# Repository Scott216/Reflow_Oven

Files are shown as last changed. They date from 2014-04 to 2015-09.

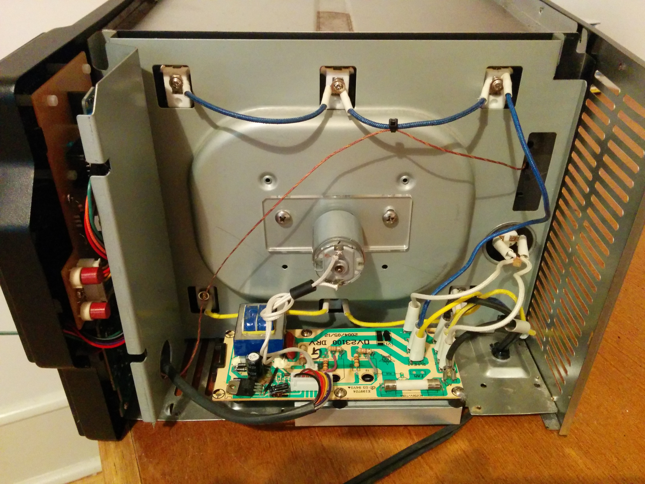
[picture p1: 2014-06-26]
Photos/Open Side.jpg

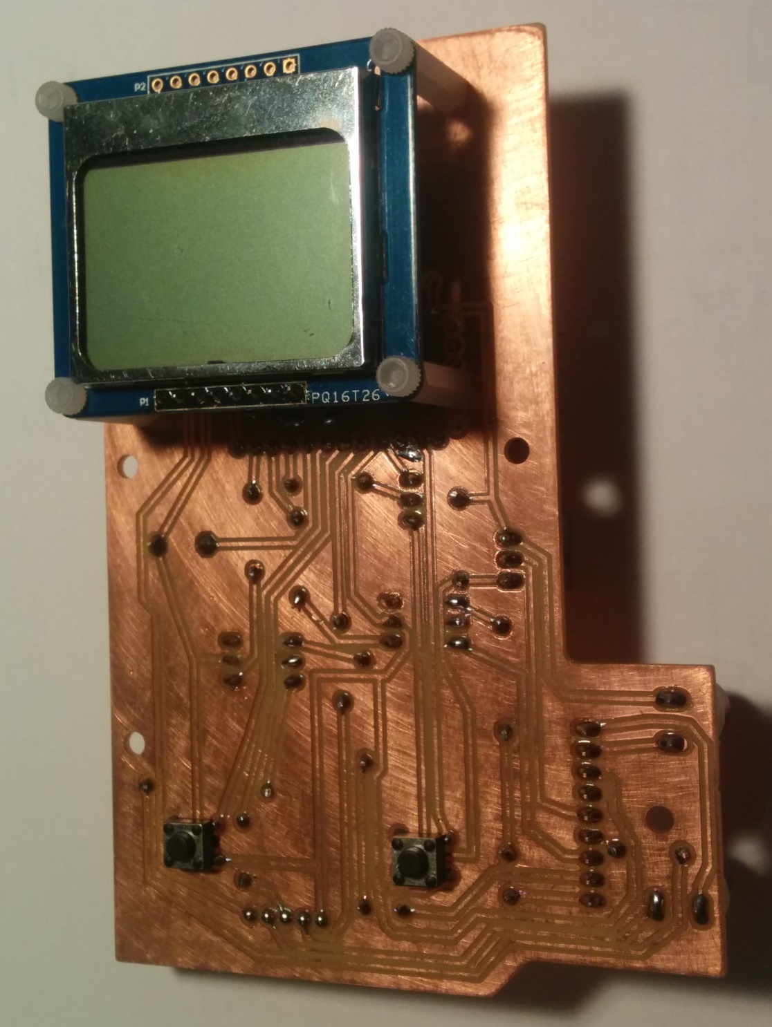
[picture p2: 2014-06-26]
Photos/PCB Traces.jpg

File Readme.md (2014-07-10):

Reflow Oven Controller <br>

I found a nice toaster oven when I when I was dropping some garbage off at our town's e-waste dumpster.  It was in excellent condition.  It has heating three heating elements on the top and three on the bottom . It had a microcontroller to control everything, so it was a bit more complex then a toaster with just a couple of knobs.  My plan was to remove the micro controller PCB and replace it with my own.  The heating elements are controlled by a couple of (triacs BTA26-600B).  I hadn't used triacs before and had to do a little research on them.  One unusual aspect of the toaster design is that the microcontroller board was floating on the 110 VAC line.  This means that the 5 VDC supply voltage was over 100 volts if measure from mains ground.  But the digital ground was only 5 volts less.  So to the micro controller board this was fine, but the whole PCB was essentially about 110 VAC.  I wasn't really comfortable with this, so I hacked the power supply board a bit so it output straight 5 volts.  it also output -9 volts. <br>

I wanted to continue to use the big start button from the front panel, so I took the original micro controller PCB and cut it in half to keep the start button and the LEDs that lit it up.  Then I soldered some wires in a header that connected to the button and LEDs.<br>

I designed a PCB with Cadsoft Eagle and milled it out on my [ShapeOko](http://www.shapeoko.com/) CNC router.  This was one of the first PCBs I did on the ShapeOko and it turned out pretty well (after a few revs). 
I had to figure out how to trigger the triacs properly.  At first I didn't realize I had to trigger when the AC voltage crossed zero volts, this cause some magic smoke to be released from one of the resistors.  This was easily fixed.  Then I got a couple of Fairchild [MOC3032](http://www.digikey.com/product-search/en?keywords=MOC3032M-ND) zero-crossover opto-couplers.  I had a Nokia 5110 display from Adafruit which was a great fit for the existing display window.  I used an Arduino [Pro-mini](http://www.sparkfun.com/products/11114) (3.3 v) from Sparkfun to control everything.  To measure the temperature I have a [thermocouple](http://www.adafruit.com/products/270) from Adafruit and Adafruit's [thermocouple amplifier](http://www.adafruit.com/products/269).  <br>

For the Arduino code I started with code from here: http://github.com/CvW/Reflow-Oven-Controller/, which is based on code from [Rocketscream](http://github.com/rocketscream/Reflow-Oven-Controller).  There was a bug in the debounce code I fixed and I replaced the MAX6675 with MAX31855 thermocouple amplifier.   There a bunch of other little changes, nothing major.  The code has two solder temperature profiles that you can choose between (by pressing the bake button) - one for leaded paste and one for a low-temp paste <br>

This toaster is not a convection toaster where it circulates the air around, but I thought this would be a nice feature. So I used a little motor that I salvaged from an inkjet printer to power a 3.5 inch aluminum fan blade I ordered from McMaster (17545K63).  I used a 3/16 bronze flange busing (McMaster 9440T63) to support the brass shaft through the sheet metal side. The fan is a bit noisy, but works pretty well.  Since the reflow oven isn't an that long, not a lot of heat is conducted to the motor from the shaft. <br>  

I would like to have an interior light to illuminate the PCB as it's being reflowed, but I haven't figured out how to do that yet. <br>

You can see some pictures on [flickr](https://www.flickr.com/photos/37101040@N00/sets/72157645550432296/) or in the \photos directory of the repo. <br>

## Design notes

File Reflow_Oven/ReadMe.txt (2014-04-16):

Reflow Oven Controller
Based on  https://github.com/CvW/Reflow-Oven-Controller/blob/master/reflowOvenController.pde
Which is based on http://github.com/rocketscream/Reflow-Oven-Controller

BoM

1x Arduino Pro-Mini 3.3 volts https://www.sparkfun.com/products/11114
1x LCD Display monochrome 84x84 http://www.adafruit.com/products/338
1x Red LED
1x Green LED
1x Solid State Relay
1x Fuse Holder
1x Fuse
1x Thermocouple Breakout board http://www.adafruit.com/products/269
1x Thermocouple probe
1x Contactless IR sensor http://www.adafruit.com/products/1747
2x pushbuttons
1x Diode for motor noise reduction
1x Cap for motor noise reduction
1x MOSFET to run motor
2x Strip heter, McMaster 3619K831
2ft Oven Wire
Calcium Silicate Insulation McMaster 9353K32 9353K31
1x High temp gasketing adhesive McMaster 7573A63
1x DC Motor
1x RC boat prop, metal
1x shaft Coupling
1x Thermistor Digikey KC024N-ND
1x AC/DC Converter Digikey 102-2386-ND, data sheet http://www.cui.com/product/resource/vsk-s5.pdf
1x 5v to 3v voltage regulator - might be able to use regulator in Pro-Mini
1x 1uF cap for AC/DC supply
1x 47uF cap for AC/DC supply
1x MOV Varistor
1x Relay for heater Digikey CLA394-ND, 6 amp, Input: 1.2 volts 1.5mA  Datasheet http://www.clare.com/home/pdfs.nsf/www/CPC1907B.pdf/$file/CPC1907B.pdf
1x 1.5k Resistor for Relay
1x Buzzer
2x I2C pullup resistors

To Do: 
See if buzzer works on 3v

PCB Design
Have 4 port terminal block in case you want to use IR sesnsor, it's I2C
Power thermocouple breakout board on 3 volt Vo pin - verify this will work

1       1       1       0
26      130.00          27.00           1       1       1       0
27.00   30.00   -0.60   0       -60
27      130.00          26.75           1       1       1       0
28      130.00          26.50           1       1       1       0
29      130.00          26.50           1       1       1       0
30      130.00          26.25           1       1       1       0
31      130.00          26.00           1       1       1       0
26.00   27.00   -0.20   0       -20
32      130.00          26.00           1       1       1       0
33      130.00          26.00

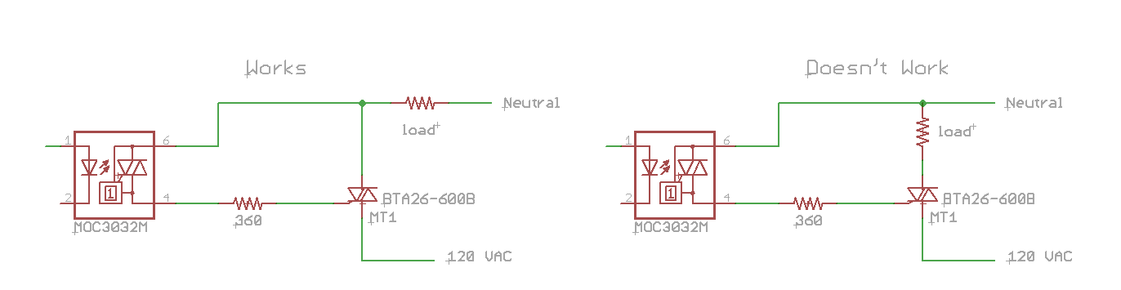
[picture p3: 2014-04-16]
Zero Crossing Triac Cuircuit 2.png

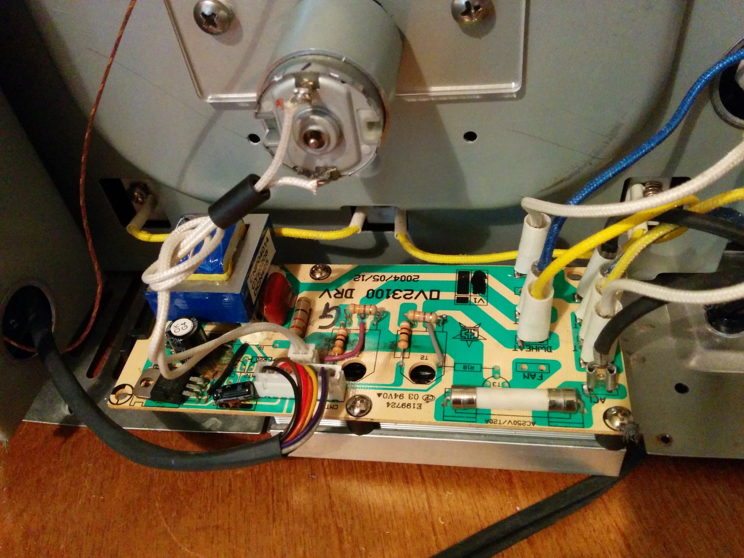
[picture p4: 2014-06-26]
Photos/Power Supply.jpg

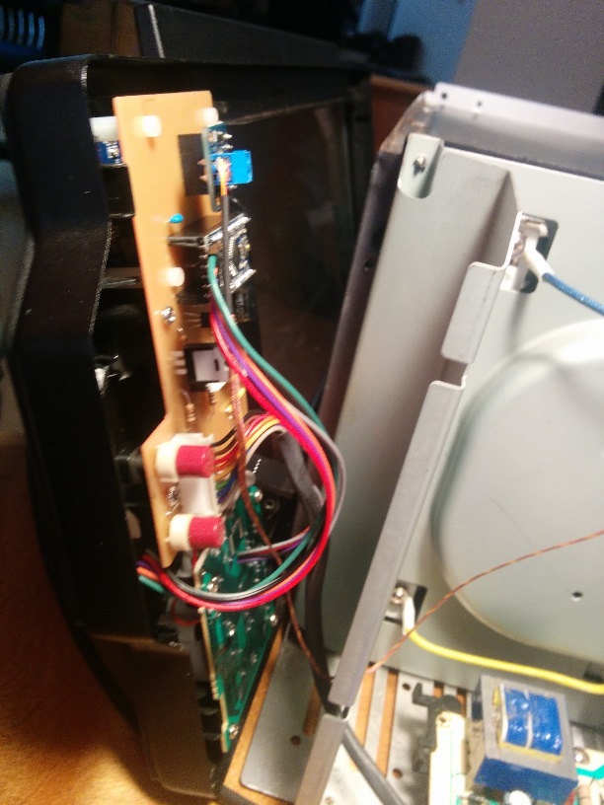
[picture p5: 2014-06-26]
Photos/Mounted PCB 2.jpg

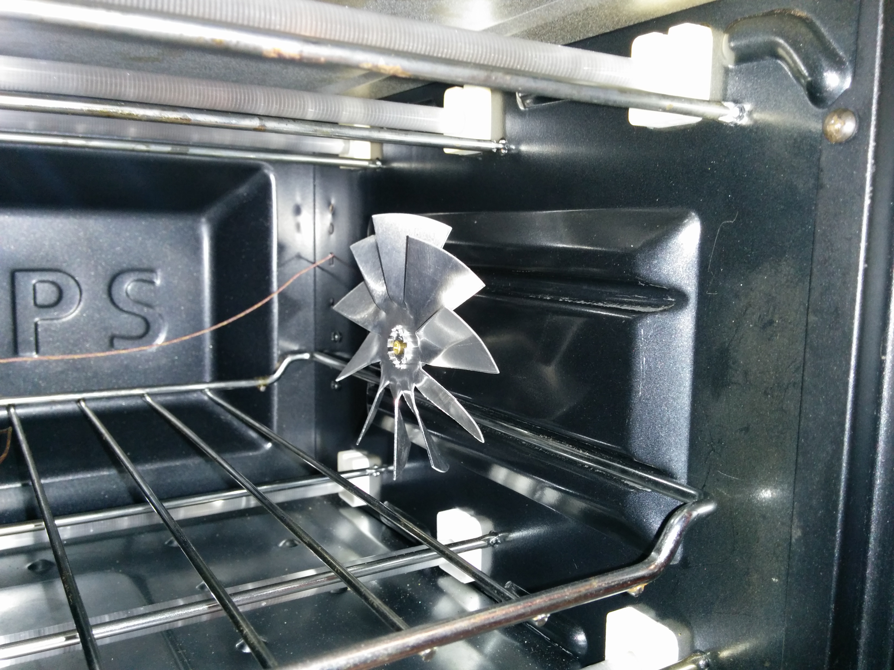
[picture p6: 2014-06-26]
Photos/Convection Fan.jpg

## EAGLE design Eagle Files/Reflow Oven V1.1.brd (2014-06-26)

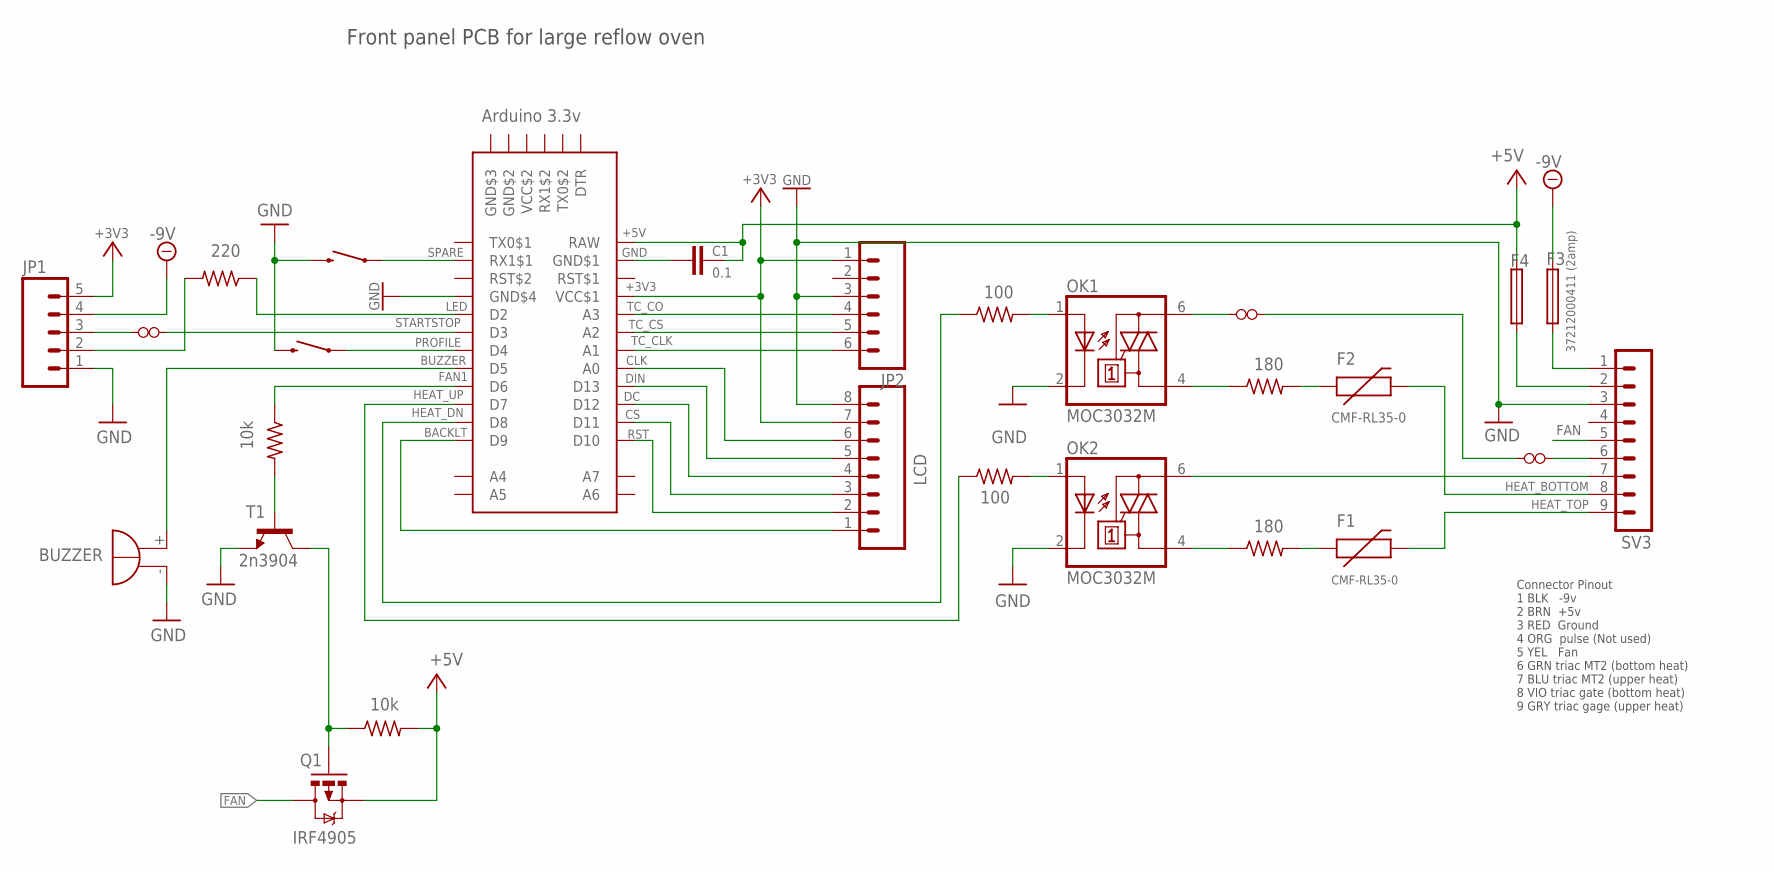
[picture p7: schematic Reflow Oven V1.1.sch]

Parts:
BUZZER: F/HMB
C1: 0.1; CAP-PTH-SMALL
F1, F2: CMF-RL35-0; PTC
F3, F4: 37212000411 (2amp); 19560
JP1: M05PTH; 1X05
JP2: M06SIP; 1X06
LCD: M081X08; 1X08
OK1, OK2: MOC3032M; DIL06
PROFILE: SWITCH-MOMENTARY-2PTH; TACTILE-PTH
Q1: IRF4905; TO220V
R2, R5: 100; 0207/10
R3, R4: 180; 0207/12
R11, R13: 10k; 0207/10
R12: 220; 0207/10
SPARE: SWITCH-MOMENTARY-2PTH; TACTILE-PTH
SV3: MA09-1
T1: 2n3904; TO92-EBC
U$1, U$4: JUMPER0.3_INCH; JUMPER_0.3
U$2: Arduino 3.3v; ARDUINO_PRO_MINI
U$5: JUMPER0.7INCH; JUMPER_0.7

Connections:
+3V3: JP1.5, JP2.1, LCD.7, U$2.VCC$1
+5V: C1.1, F4.2, Q1.3 (S), R13.2, U$2.RAW
-9V: F3.2, JP1.4
BACKLT: LCD.1, U$2.D9
BUZZER: BUZZER.+, U$2.D5
CLK: LCD.6, U$2.A0
CS: LCD.3, U$2.D11
DC: LCD.4, U$2.D12
DIN: LCD.5, U$2.D13
FAN: Q1.2 (D), SV3.5
FAN1: R11.1, U$2.D6
F_GATE: Q1.1 (G), R13.1, T1.C
GND: BUZZER.-, JP1.1, JP2.3, LCD.8, OK1.2 (C), OK2.2 (C), PROFILE.3 (2), SPARE.3 (2), SV3.3, T1.E, U$2.GND$4
GND2: C1.2, U$2.GDN$1 (GND$1)
GND$2: U$2.GND$2
GND$3: U$2.GND$3
HEAT_BOTTOM: F2.P$2 (2), SV3.8
HEAT_DN: R5.1, U$2.D8
HEAT_TOP: F1.P$2 (2), SV3.9
HEAT_UP: R2.1, U$2.D7
LED: R12.1, U$2.D2
unnamed: OK1.4 (A1), R3.1
unnamed: OK2.6 (A2), SV3.7
unnamed: F2.P$1 (1), R3.2
unnamed: F4.1, SV3.2
unnamed: F1.P$1 (1), R4.2
unnamed: OK2.4 (A1), R4.1
unnamed: U$1.P$1, U$5.P$2
unnamed: SV3.6, U$1.P$2
unnamed: OK1.1 (A), R5.2
unnamed: OK1.6 (A2), U$5.P$1
unnamed: OK2.1 (A), R2.2
unnamed: JP1.3, U$4.P$1
unnamed: F3.1, SV3.1
unnamed: R11.2, T1.B
unnamed: JP1.2, R12.2
PROFILE: PROFILE.1, U$2.D4
RST: LCD.2, U$2.D10
SPARE: SPARE.1, U$2.RX1$1
STARTSTOP: U$2.D3, U$4.P$2
TC_CLK: JP2.6, U$2.A1
TC_CO: JP2.4, U$2.A3
TC_CS: JP2.5, U$2.A2
VCC$2: U$2.VCC$2

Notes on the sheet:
Front panel PCB for large reflow oven
Connector Pinout 1 BLK -9v 2 BRN +5v 3 RED Ground 4 ORG pulse (Not used) 5 YEL Fan 6 GRN triac MT2 (bottom heat) 7 BLU triac MT2 (upper heat) 8 VIO triac gate (bottom heat) 9 GRY triac gage (upper heat)

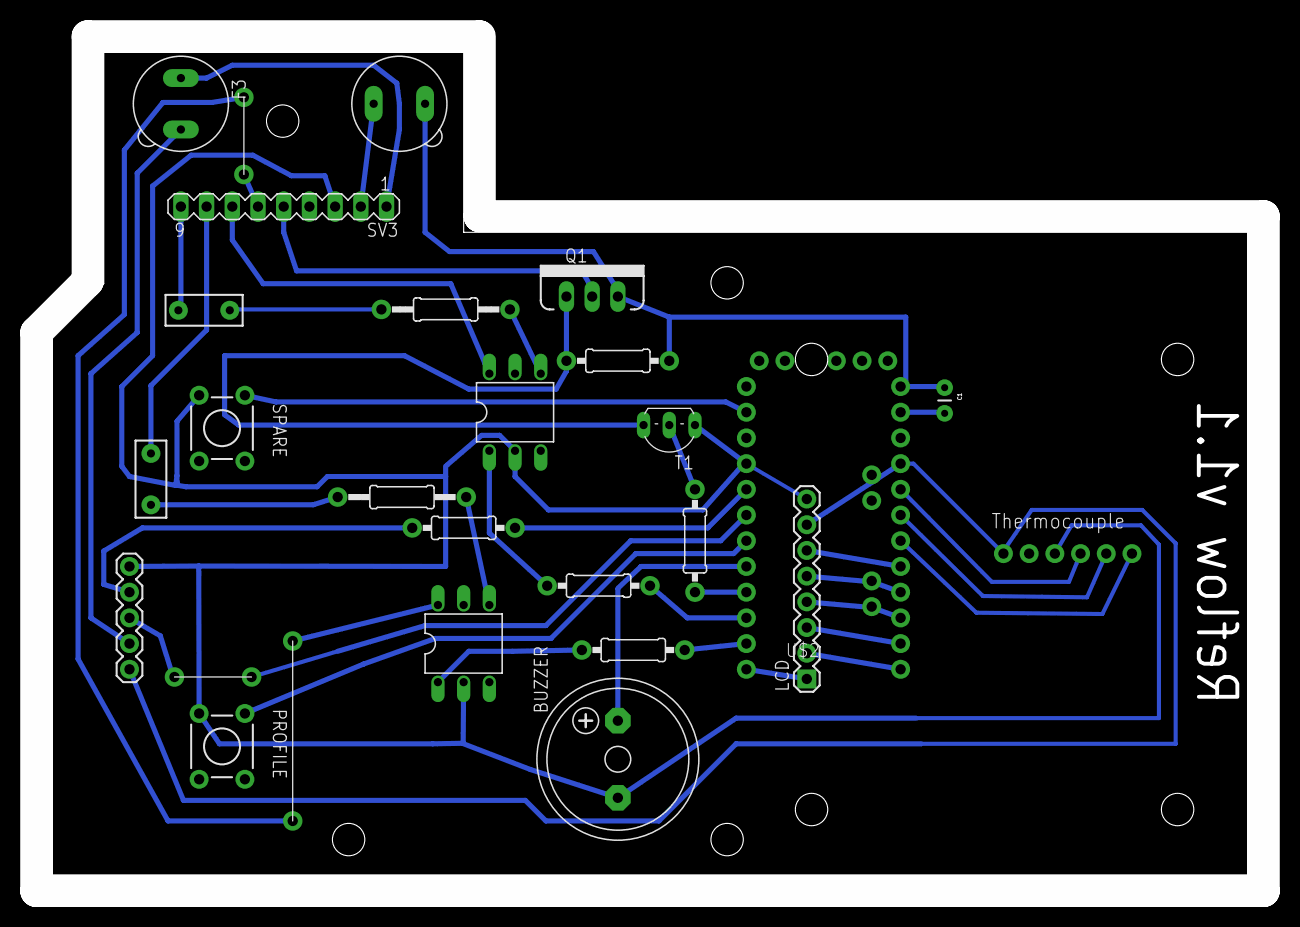
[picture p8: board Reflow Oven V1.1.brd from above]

Board: 2 copper layers, 121.3 x 84.5 mm, 27 parts (1 on the bottom side), 41 nets.

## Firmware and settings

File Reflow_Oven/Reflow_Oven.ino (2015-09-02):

// Uses Arduino ProMini 3.3 volts

// to do
// had hall effect sensor to detect fan current and shut down if too high - maybe
// put a switch on the fan - maybel
// PCB Circuit swaps D2 and D4
// Put limits on setpoints so they cont go to high if there is a problem

/*******************************************************************************
 * Title: Reflow Oven Controller
 * Company: Rocket Scream Electronics
 * Original Author: Lim Phang Moh
 * Website: www.rocketscream.com
 * 
 * Brief
 * =====
 * This is an example firmware for our Arduino compatible reflow oven controller. 
 * The reflow curve used in this firmware is meant for lead-free profile 
 * (it's even easier for leaded process!). You'll need to use the MAX31855 
 * library for Arduino if you are having a shield of v1.60 & above which can be 
 * downloaded from our GitHub repository. Please check our wiki 
 * http://www.rocketscream.com/wiki for more information on using this piece of code 
 * together with the reflow oven controller shield. 
 *
 * Temperature (Degree Celcius)                 Magic Happens Here!
 * 245-|                                               x  x  
 *     |                                            x        x
 *     |                                         x              x
 *     |                                      x                    x
 * 200-|                                   x                          x
 *     |                              x    |                          |   x   
 *     |                         x         |                          |       x
 *     |                    x              |                          |
 * 150-|               x                   |                          |
 *     |             x |                   |                          |
 *     |           x   |                   |                          | 
 *     |         x     |                   |                          | 
 *     |       x       |                   |                          | 
 *     |     x         |                   |                          |
 *     |   x           |                   |                          |
 * 30 -| x             |                   |                          |
 *     |<  60 - 90 s  >|<    90 - 120 s   >|<       90 - 120 s       >|
 *     | Preheat Stage |   Soaking Stage   |       Reflow Stage       | Cool
 *  0  |_ _ _ _ _ _ _ _|_ _ _ _ _ _ _ _ _ _|_ _ _ _ _ _ _ _ _ _ _ _ _ _ _ _ _ _ 
 *                                 Time (Seconds)
 *
 * Kester's standard leaded profile http://www.kester.com/kester-content/uploads/2013/06/Standard_Profile.pdf
 * This firmware owed very much on the works of other talented individuals as
 * follows:
 * ==========================================
 * Brett Beauregard (www.brettbeauregard.com)
 * ==========================================
 * Author of Arduino PID library. On top of providing industry standard PID 
 * implementation, he gave a lot of help in making this reflow oven controller 
 * possible using his awesome library.
 *
 *
 * Disclaimer
 * ==========
 * Dealing with high voltage is a very dangerous act! Please make sure you know
 * what you are dealing with and have proper knowledge before hand. Your use of 
 * any information or materials on this reflow oven controller is entirely at 
 * your own risk, for which we shall not be liable. 
 *
 * Licences
 * ========
 * This reflow oven controller hardware and firmware are released under the 
 * Creative Commons Share Alike v3.0 license
 * http://creativecommons.org/licenses/by-sa/3.0/ 
 * You are free to take this piece of code, use it and modify it. 
 * All we ask is attribution including the supporting libraries used in this 
 * firmware. 
 *
 *
 * Source: http://github.com/CvW/Reflow-Oven-Controller/blob/master/reflowOvenController.pde
 * Which is based on http://github.com/rocketscream/Reflow-Oven-Controller
 *
 * Info on PID: http://brettbeauregard.com/blog/2011/04/improving-the-beginners-pid-introduction/
 * Build instructions: http://www.rocketscream.com/blog/portfolio-item/reflow-controller-shield
 *
 *
 * Rocket Scream Revisions
 * Revision  Description
 * ========  ===========
 * 1.20			Adds supports for v1.60 (and above) of Reflow Oven Controller 
 *           Shield:
 *					  - Uses MAX31855KASA+ chip and pin reassign (allowing A4 & A5 (I2C)
 *             to be used for user application).
 *					  - Uses analog based switch (allowing D2 & D3 to be used for user 
 *						  application).	
 *						Adds waiting state when temperature too hot to start reflow process.
 *						Corrected thermocouple disconnect error interpretation (MAX6675).
 * 1.10      Arduino IDE 1.0 compatible.
 * 1.00      Initial public release.
 *
 *
 * CvW Revisions
 * Revision  Description
 * ========  ===========
 * 1.20      Added option for lead solder profile, Enabled fan motor, added error message
 * 1.10      Arduino IDE 1.0 compatible.
 * 1.00      Initial public release.
 *
 * Scott216 Revisions
 * Revision  Description
 * ========  ===========
 * 1.21      Started with CvW version 1.2 and replaced MAX6675 library with Adafruit_MAX31855, changed some formatting
 * 1.22      Moved LCD display code to separate function, added NAN error checking on thermocouple, changed profiles to leaded and low temp, changed LED output so HIGH is on
 * 1.23      Took typedef out of enum, moved buttons to D0 & D1 because of I2C conflict, changed I2C library.  Removed debounce for button #2, it was causing problems where btn1 would make btn2 code run
 * 1.24      Updated profile temperatures, moved some code out of loop() into functions, removed 2 line LCD code.  Added seconds and rate to LCD display.  Changed some variables.
 * 1.25      Change pins for Pro-Mini, changed C/Sec to average over 5 seconds
 * 1.26      Changed display to Nokia 5110, tested for negative rate change so it will display properly
 * 1.27      Changed I/O pins, added pin for LED backlight
 * 1.28      When calling for heat, top and bottom heaters will altenrate coming on.
 * 1.29      Reversed LED output (Low = on), made display text 3 lines.  Changed fan from digital to PWM
 * 1.30      Buzzer sounds and each stage in reflow.  Adjusted heat on to better balance top and bottom heaters, display profile when idle
 * 1.31      Added mircostepping temp target to pre-heat stage, show setpoint temp in display
 * 1.32      Fan was not turning off after cool period was over, should be fixed now 
 * 1.33      Changed contrast, moved inputs to match new PCB
 * 1.34      Adjusted contrast
 * 1.35      Adjusted contrast again, added more beeps when cooling stage starts 
 * 1.36      Changed constast from 40 to 50.  Added FAN_OFF constant
 * 1.37      Added max setpoint to prevent run-away temp, renamed global variables
 
 *******************************************************************************/
#define VERSION  "ver 1.37"

#include "Adafruit_MAX31855.h"  // http://github.com/adafruit/Adafruit-MAX31855-library
#include "PID_v1.h"             // http://github.com/br3ttb/Arduino-PID-Library/
#include "Adafruit_GFX.h"       // https://github.com/adafruit/Adafruit-GFX-Library
#include "Adafruit_PCD8544.h"   // http://github.com/adafruit/Adafruit-PCD8544-Nokia-5110-LCD-library


// ***** TYPE DEFINITIONS *****
enum reflowState_t
{
  REFLOW_STATE_IDLE,
  REFLOW_STATE_PREHEAT,
  REFLOW_STATE_SOAK,
  REFLOW_STATE_REFLOW,
  REFLOW_STATE_COOL,
  REFLOW_STATE_COMPLETE,
  REFLOW_STATE_ERROR
};

enum reflowStatus_t
{
  REFLOW_STATUS_OFF,
  REFLOW_STATUS_ON
};

enum debounceState_t
{
  DEBOUNCE_STATE_IDLE,
  DEBOUNCE_STATE_CHECK,
  DEBOUNCE_STATE_RELEASE
} ;

enum printData_t { PRINT_HEADER, PRINT_DATA};
  
// ***** CONSTANTS *****
#define TEMPERATURE_ROOM             50   // Temp must be below this to start a new reflow
#define SENSOR_SAMPLING_TIME       1000
#define PREHT_TEMPERATURE_STEP        5   // increment pre-heat temp in 5 degree steps
#define SOAK_TEMPERATURE_STEP         5   // increment soak temp in 5 degree steps
#define PREHT_MICRO_PERIOD         4250   // set new pre-heat target temp every 4-1/4 seconds
#define SOAK_MICRO_PERIOD          9000   // set new soak target temp evey 9 seconds
#define DEBOUNCE_PERIOD_MIN          50
#define MAX_ALLOWED_TEMP            250  // Max temp oven is allowed to go, Centegrade

// Below temperature constants are for Pb-Free Operation
enum solderProfile_t
{
  LEADED_PROFILE,   // Henkel multicore 583489 (Digikey 82-143-ND), Melts 183°C
  LOWTEMP_PROFILE   // Chip Quik SMDLTLFP (Digikey SMDLTLFP-ND), Melts at 138°C
};

solderProfile_t solderType = LEADED_PROFILE; // used in arrays to choose which profile is being used, default to leaded

// Define profiles.  First element is leaded, 2nd is low temp
// Solder Info:  https://tds.us.henkel.com/NA/UT/HNAUTTDS.nsf/web/B5E62B506B289ABA882571870000DBBB/$File/MP200.pdf
// Leaded Solder: Henkel multicore 583489 (Digikey 82-143-ND)
// Data Sheet
// Desired Profile:
//   Preheat:     120 sec, 130-165°C
//   Soaking:     120 sec, 130-165°C
//   Reflow:    30-75 sec, 205-225°C
//   Cooling:     25+ sec, 100°C

// Low Temp Solder: Chip Quik SMDLTLFP Sn42Bi58 (42/58) (Digikey SMDLTLFP-ND)
// Low Temp Profile:
//   Preheat:     120 sec, 90-120°C
//   Soaking:   60-90 sec, 90-130°C
//   Reflow:    30-60 sec, 158-165°C
//   Cooling:     15+ sec, 100°C
//
// Leaded solder: Multicore 583489, Digikey 82-143-ND,
// Leaded Profile
//   Preheat:    60-90 sec, 130-165°C
//   Soaking:   60-120 sec, 130-165°C
//   Reflow:    90-120 sec, 205-225°C
//   Cooling:      15+ sec, 100°C
// Data Sheet  http://bit.ly/1cRVSGo
//                             Leaded   Low Temp
int TEMPERATURE_SOAK_MIN[] =   {130,       90};
int TEMPERATURE_SOAK_MAX[] =   {165,      130};
int TEMPERATURE_REFLOW_MAX[] = {220,      165};
int TEMPERATURE_COOL_MIN[] =   {100,      100};
// Controller will heat up to TEMPERATURE_SOAK_MIN, this is the preheat stage.  When it reaches this temperature, the soak stage starts.
// Soak stage increases setpoint temp 5°C (SOAK_TEMPERATURE_STEP) every 9 seconds (SOAK_MICRO_PERIOD).  Then goes into reflow stage
// Controller will then heat until TEMPERATURE_REFLOW_MAX is reached, then cooling stage starts.
// Cooling continues until temp is TEMPERATURE_COOL_MIN


// ***** PID PARAMETERS *****
// ***** PRE-HEAT STAGE *****
#define PID_KP_PREHEAT   300
#define PID_KI_PREHEAT  0.05
#define PID_KD_PREHEAT   400
// ***** SOAKING STAGE *****
#define PID_KP_SOAK      300
#define PID_KI_SOAK     0.05
#define PID_KD_SOAK      250
// ***** REFLOW STAGE *****
#define PID_KP_REFLOW    300
#define PID_KI_REFLOW   0.05
#define PID_KD_REFLOW    350
#define PID_SAMPLE_TIME 1000

// ***** LCD MESSAGES *****
const char* lcdMessagesReflowStatus[] = {"Ready", "Pre-heat", "Soak", "Reflow", "Cool", "Complete", "Error" };

// Pro Mini Pin Assignemts
// Thermocouple Breakout
const int thermocoupleSO =  A3;
const int thermocoupleCS =  A2;
const int thermocoupleCLK = A1;

// I/O
const int spareBtn =          1;  // Spare pushbutton
const int changeProfileBtn  = 4;  // Change profile button, , on interrupt pin (in case you want to use them
const int cycleStartStopBtn = 3;  // Start-stop button, on interrupt pin (in case you want to use them
const int grnLED =            2;  // Blinks when oven is on
const int buzzer =            5;  // PWM pin - useful if you want to use a piezo buzzer
const int fan =               6;  // PWM pin
const int heater_top =        7;
const int heater_bottom =     8;

// LCD Display
const int dispLED =            9; // pull low to turn backlight off, PWM pin
const int dispClk =           A0;
const int dispDin =           13;
const int dispDC =            12;
const int dispCS =            11;
const int dispRst =           10;

// Spare D0, A4, A5, A6, A7

const int ledOn = LOW;   // green LEDs on original circuit board are on when LOW (uses PNP transistor)
const int ledOff = HIGH;
const byte FAN_ON = 255;
const byte FAN_OFF =  0; 

// ***** PID CONTROL VARIABLES *****
double g_pid_setpoint;
double g_pid_input;
double g_pid_output;

const int windowSize = 2000;     // Set PID window size
uint32_t windowStartTime;
uint32_t nextCheck;
uint32_t nextRead;
uint32_t timerPreHeat;           // Timer used for micro-stepping setpoint in Pre-heat stage
uint32_t timerSoak;              // Timer used for micro-stepping setpoint in Soak stage
uint32_t buzzerPeriod;           // Time for buzzer


reflowState_t   reflowState;           // Reflow oven controller state machine state variable
reflowStatus_t  reflowStatus;          // Reflow oven controller status
debounceState_t debounceState;         // Button debounce state machine state variable
uint32_t        lastDebounceTime;      // Button debounce timer
bool            cycleStartStopStatus;  // Button press status
int             timerSeconds;          // Seconds timer

// Specify PID control interface
PID reflowOvenPID(&g_pid_input, &g_pid_output, &g_pid_setpoint, PID_KP_PREHEAT, PID_KI_PREHEAT, PID_KD_PREHEAT, DIRECT);

// Adafruit_SSD1306 display(dispRst);
Adafruit_PCD8544 display = Adafruit_PCD8544(dispClk, dispDin, dispDC, dispCS, dispRst);


// Specify thermocouple interface
Adafruit_MAX31855 thermocouple(thermocoupleCLK, thermocoupleCS, thermocoupleSO);


// Function Prototypes
void getTemperature();
void checkButtons();
void lcdDisplay(int line, const char *lcdText);
void setHeatOn();
void setHeatOff();
void printData(printData_t whatToPrint);


//==============================================================================================================================
//==============================================================================================================================
void setup()
{
  // Configure I/O pins
  pinMode(dispLED,                 OUTPUT);  // pwm output
  pinMode(heater_top,              OUTPUT);
  pinMode(heater_bottom,           OUTPUT);
  pinMode(fan,                     OUTPUT);  // pwm output
  pinMode(buzzer,                  OUTPUT);
  pinMode(grnLED,                  OUTPUT);
  pinMode(cycleStartStopBtn, INPUT_PULLUP);
  pinMode(changeProfileBtn,  INPUT_PULLUP);
  pinMode(spareBtn,          INPUT_PULLUP);
  
  analogWrite(dispLED, 127);  // turn LCD backlignt on at 50%
  
  Serial.begin(9600);

  // Start-up
  lcdDisplay(-1, "");  // initialze display
  lcdDisplay(0, "Reflow Oven");
  lcdDisplay(1, VERSION);
  digitalWrite(buzzer, HIGH);
  delay(500);
  digitalWrite(buzzer, LOW);
  delay(1500);
  
  nextCheck = millis();  // Initialize time keeping variable
  nextRead =  millis();  // Initialize thermocouple reading varible

  Serial.println("Finished setup");
  
}  // end setup()
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

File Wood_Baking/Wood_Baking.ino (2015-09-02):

/*
Uses Arduino ProMini 3.3 volts
Use reflow oven to cure wood stabilizer in pen blanks
Bake at 93C for 40 minutes



Change Log
08/14/15  ver 1.00  Initial Version.  Tried to incorporate this into the reflow code, but I couldn't get it to work
08/15/15  ver 1.01  Made change so finished buzzer doesn't keep going off

*/


#define VERSION  "ver 1.00"

#include "Adafruit_MAX31855.h"  // http://github.com/adafruit/Adafruit-MAX31855-library
#include "PID_v1.h"             // http://github.com/br3ttb/Arduino-PID-Library/
#include "Adafruit_GFX.h"       // https://github.com/adafruit/Adafruit-GFX-Library
#include "Adafruit_PCD8544.h"   // http://github.com/adafruit/Adafruit-PCD8544-Nokia-5110-LCD-library



// Pro Mini Pin Assignemts
// Thermocouple Breakout
const int thermocoupleSO =  A3;
const int thermocoupleCS =  A2;
const int thermocoupleCLK = A1;

// I/O
const int spareBtn =          1;  // Spare pushbutton
const int changeProfileBtn  = 4;  // Change profile button, , on interrupt pin (in case you want to use them
const int cycleStartStopBtn = 3;  // Start-stop button, on interrupt pin (in case you want to use them
const int grnLED =            2;  // Blinks when oven is on
const int buzzer =            5;  // PWM pin - useful if you want to use a piezo buzzer
const int fan =               6;  // PWM pin
const int heater_top =        7;
const int heater_bottom =     8;

// LCD Display
const int dispLED =            9; // pull low to turn backlight off, PWM pin
const int dispClk =           A0;
const int dispDin =           13;
const int dispDC =            12;
const int dispCS =            11;
const int dispRst =           10;

const byte BUTTON_PRESSED = LOW;  
const uint16_t DEBOUNCE_TIME = 300;  // button debounce time in mS


const int ledOn =   LOW;   // green LEDs on original circuit board are on when LOW (uses PNP transistor)
const int ledOff = HIGH;
const byte FAN_ON = 255;
const byte FAN_OFF =  0;
const byte OVEN_ON =  1;
const byte OVEN_OFF = 0;


// ***** PID CONTROL VARIABLES *****
double g_setpoint = 93;
double g_input;
double g_output;

// ***** PID PARAMETERS *****
#define PID_KP                 300
#define PID_KI                   0.05
#define PID_KD                 350
#define PID_SAMPLE_TIME       1000
#define SENSOR_SAMPLING_TIME  1000


// Specify PID control interface
PID OvenPID(&g_input, &g_output, &g_setpoint, PID_KP, PID_KI, PID_KD, DIRECT);

// Adafruit_SSD1306 display(dispRst);
Adafruit_PCD8544 display = Adafruit_PCD8544(dispClk, dispDin, dispDC, dispCS, dispRst);

// Specify thermocouple interface
Adafruit_MAX31855 thermocouple(thermocoupleCLK, thermocoupleCS, thermocoupleSO);

// Function Prototypes
void getTemperature();
void setHeatOn();
void setHeatOff();


//==============================================================================================================================
//==============================================================================================================================
void setup()
{
  Serial.begin(9600);

  // Configure I/O pins
  pinMode(dispLED,                 OUTPUT);  // pwm output
  pinMode(heater_top,              OUTPUT);
  pinMode(heater_bottom,           OUTPUT);
  pinMode(fan,                     OUTPUT);  // pwm output
  pinMode(buzzer,                  OUTPUT);
  pinMode(grnLED,                  OUTPUT);
  pinMode(cycleStartStopBtn, INPUT_PULLUP);
  pinMode(changeProfileBtn,  INPUT_PULLUP);
  pinMode(spareBtn,          INPUT_PULLUP);
  
  analogWrite(dispLED, 127);  // turn LCD backlignt on at 50%
  analogWrite(fan, FAN_OFF);

  BuzzerChirp();
  BuzzerChirp();

  display.begin();
  display.setTextSize(1);
  display.setTextColor(BLACK);
  display.setContrast(50);
  display.clearDisplay(); 
  display.setCursor(0, 11);
  display.print("Bake Wood");
  display.setCursor(0, 22);
  display.print(VERSION);
  display.display();
  delay(1500);   // time to read display before it changes 
  
  Serial.println("Bake Wood");
  Serial.println(VERSION);

}  // end setup()


//==============================================================================================================================
//==============================================================================================================================
void loop() 
{
  static byte ovenStatus =   OVEN_OFF; 
  const int windowSize =         2000;     // PID window size
  static uint32_t windowStartTime = 0;
  static uint32_t ovenStartTime = 0;
  
  getTemperature();
  
  // check for start button press
  if (digitalRead(cycleStartStopBtn) == BUTTON_PRESSED  && ovenStatus == OVEN_OFF )
  {
    ovenStatus = OVEN_ON;
    windowStartTime = millis();  // Initialize PID control window starting time
    // Tell the PID to range between 0 and the full window size
    OvenPID.SetOutputLimits(0, windowSize);
    OvenPID.SetSampleTime(PID_SAMPLE_TIME);
    OvenPID.SetMode(AUTOMATIC);  // Turn the PID on
    ovenStartTime = millis(); 
    BuzzerChirp();
    delay(DEBOUNCE_TIME);
  }
  
  // check for button press to stop oven
  if (digitalRead(cycleStartStopBtn) == BUTTON_PRESSED  && ovenStatus == OVEN_ON )
  {
    ovenStatus = OVEN_OFF;
    BuzzerChirp();
    delay(DEBOUNCE_TIME);
  }

  // Reached end of baking cycle
  if ((long)(millis() - ovenStartTime) > 2400000UL && (ovenStatus == OVEN_ON))
  {
    ovenStatus = OVEN_OFF;
    display.clearDisplay(); 
    display.setCursor(0, 11);
    display.print("Finished!");
    display.display();
    BuzzerChirp();
    delay(200);
    BuzzerChirp();
    delay(200);
    BuzzerChirp();
    delay(6000);    
  }
  

  char buf[20];
  if (ovenStatus == OVEN_OFF)
  {
    sprintf(buf, "%dC", (int) g_input);  // current temperature
    
    display.clearDisplay(); 
    display.setCursor(0, 11);
    display.print("Ready");
    display.setCursor(0, 22);
    display.print(buf);
    display.display();
  }

  if (ovenStatus == OVEN_ON)
  {
    sprintf(buf, "%dC  %d Min", (int) g_input, (int) ((millis() - ovenStartTime)/60000));  // current temperature
    
    display.clearDisplay(); 
    display.setCursor(0, 11);
    display.print("Oven On");
    display.setCursor(0, 22);
    display.print(buf);
    display.display();
  }
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

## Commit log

2014-03-07 Based on RocketScream version
    Based on Rocketscream’s version. Removed MAX6675 and used Adafruit’s
    MAX31855 library.
2014-03-07 Switched to CvW version
    Rev 1.21. Changed to CvW version which has two profiles. Replaced
    MAX6675 with MAX31855
    [Reflow_Oven.ino]
2014-03-07 Switched to CvW version
2014-03-09 Changed LCD, profile temps, t/c errors
    v 1.22 - Moved LCD display code to separate function, added NAN error
    checking on thermocouple, changed profiles to leaded and low temp,
    changed LED output so HIGH is on
    [Reflow_Oven.ino]
2014-03-11 v1.23 - fixed button errors, changed I2C lib, moved inputs
    Took typedef out of enum, moved buttons to D0 & D1 because of I2C
    conflict, changed I2C library, removed debounce for button #2, it was
    causing wrong code to run
    [Reflow_Oven.ino]
2014-03-12 v1.24 minor changes
    Updated profile temperatures, moved some code out of loop() into
    functions, removed 2 line LCD code. Added seconds and rate to LCD
    display. Changed some variables
2014-03-12 Low Temp Solder Data Sheet
2014-04-16 Heat profile data
2014-04-25 added micro stepping for pre-heat
    Also worked on buzzer so it beeps after each stage.
    [Reflow_Oven.ino]
2014-06-26 Swapped D2 & D4, adjusted contrast
    [Reflow_Oven.ino]
2014-06-26 Eagle Files
    [Reflow Oven Other Circuits.sch, Reflow Oven V1.1.brd, Reflow Oven V1.1.sch]

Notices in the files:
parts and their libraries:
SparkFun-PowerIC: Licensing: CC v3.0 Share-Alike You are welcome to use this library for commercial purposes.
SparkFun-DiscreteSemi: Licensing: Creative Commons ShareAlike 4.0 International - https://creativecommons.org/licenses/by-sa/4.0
